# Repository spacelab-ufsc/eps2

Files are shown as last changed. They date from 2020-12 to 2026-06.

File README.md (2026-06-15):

<h1 align="center">
	ELECTRICAL POWER SYSTEM 2.0 (EPS2)
	<br>
</h1>

<p align="center">
    <!-- Versioning -->
    
    <!-- Releases -->
    
    <!-- Commits since the latest release -->
    
    <!-- Last commit -->
    
    <!-- Issues -->
    
    <!-- PRs -->
    
    <!-- Contributors -->
    
</p>

<details>
    <summary><b>Summary</b></summary>
    <ol>
        <li>
            <a href="#overview">Overview</a>
        </li>
        <li>
            <a href="#repository-organization">Repository Organization</a>
        </li>
        <li>
            <a href="#license">License</a>
        </li>
        <li>
            <a href="#releases">Releases</a>
        </li>
        <li>
            <a href="#notes">Notes</a>
        </li>
        <li>
            <a href="#references">References</a>
        </li>
    </ol>
</details>

## Repository Organization
`documentation`: Technical EPS2's documentation.

`firmware`: EPS2's firmware project (sources and configs).

`hardware`: EPS2's hardware project (sources and outputs).

## Overview
The **EPS2** [[1]](#1) was designed to collect, store, and distribute energy for GOLDS-UFSC and future SpaceLab missions, prioritizing practicality. It is highly based on the EPS1, used in FloripaSat-1 [[2]](#2). Supporting both 1U and 2U CubeSats, this EPS can interface with up to 10 solar panels attached to the structure. It operates the solar panels at their maximum power point (MPP) using the perturb and observe (P&O) technique to control three DC-DC converters at the input. The collected energy is stored in lithium-ion batteries, with power distribution managed by integrated DC-DC converters, generating 5V, 6V and 3.3V buses. This model features a microprocessor, the MSP430, which collects internal data (e.g., current, voltage, temperature) and manages their storage and transmission to the OBDH.

<p align="center">
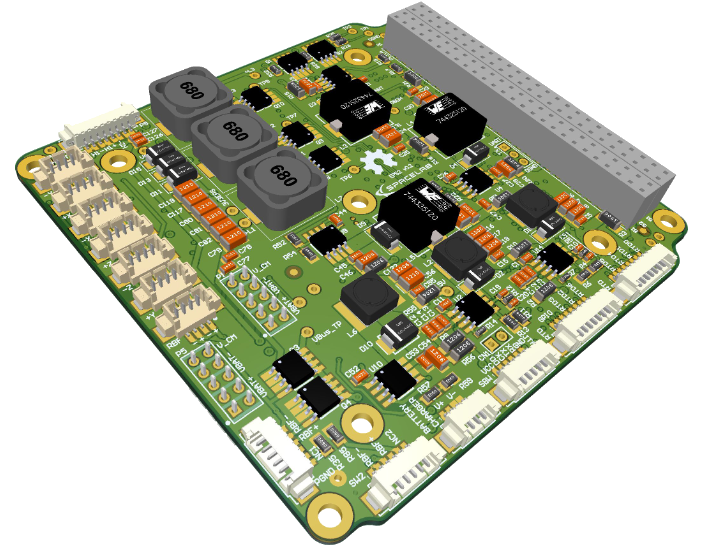
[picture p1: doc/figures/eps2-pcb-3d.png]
    
</p>

<p align="center">
    
    
    
</p>

## License
This project is open-source under three different licenses: CERN Open Hardware License v2.0 for hardware, GNU General Public License v3.0 for firmware, and CC BY-SA 4.0 for documentation.

## Releases
Releases are published after verifying that all components of the project — hardware, firmware, and documentation — are synchronized and compatible, ensuring functionality and cohesion. Using different versions of hardware, firmware, or documentation projects can lead to misunderstandings or unpredictable behavior. Please refer to the **documentation** for more details.

## Notes
For more info about the SpaceLab, access our [GitHub](https://github.com/spacelab-ufsc/spacelab), [Linkedin](https://br.linkedin.com/company/spacelab-ufsc) or our [website](https://spacelab.ufsc.br/en/home/).

## References
<a id="1">[1]</a> G. M. Marcelino, A. M. P. de Mattos, J. C. E. Barcellos, B. F. Ribeiro, L. O. Seman, E. M. Filho and E. A. Bezerra, "FloripaSat-2: An Open-Source Platform for CubeSats," in IEEE Embedded Systems Letters, vol. 16, no. 1, pp. 77-80, 2024, available at <a href="https://repositorio.ufsc.br/bitstream/handle/123456789/247559/PEEL2103-D.pdf?sequence=1&isAllowed=y"> this link</a>.

<a id="1">[2]</a> SpaceLab, "Electrical Power System (EPS)," in GitHub, 2019, available at <a href="https://github.com/spacelab-ufsc/eps"> this link</a>.

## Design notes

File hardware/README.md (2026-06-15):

<h1 align="center">
	EPS2 HARDWARE
	<br>
</h1>

<p align="center">
    <!-- Versioning -->
    
    <!-- Releases -->
    
    <!-- Hardware-related commits since the latest release -->
    
    <!-- Last hardware-related commit -->
    
    <!-- Hardware-related issues -->
    
    <!-- CAD tool used -->
    </a>
    <!-- License adopted -->
    </a>
</p>

<details>
    <summary><b>Summary</b></summary>
    <ol>
        <li>
            <a href="#overview">Overview</a>
        </li>
        <li>
            <a href="#license">License</a>
        </li>
        <li>
            <a href="#notes">Notes</a>
        </li>
        <li>
            <a href="#references">References</a>
        </li>
    </ol>
</details>

## Overview
The **EPS2** [[1]](#1) was designed to collect, store, and distribute energy for GOLDS-UFSC and future SpaceLab's missions, with a focus on practicality. It is higly based on the EPS1, used in FloripaSat-1 [[2]](#2). Then, it can be used in 1U and 2U CubeSats, this EPS can interface with up to 10 solar panels attached to the structure. It is also capable of operating the solar panels at their maximum power point (MPP). The collected energy is stored in lithium-ion batteries, and power distribution is managed by integrated DC-DC converters, generating 5V and 3.3V buses. This model is predominantly analog, enhancing its reliability in the challenging space environment. It also features redundancies in its energy harvesting unit (EHU) and power distribution unit (PDU).

<p align="center">
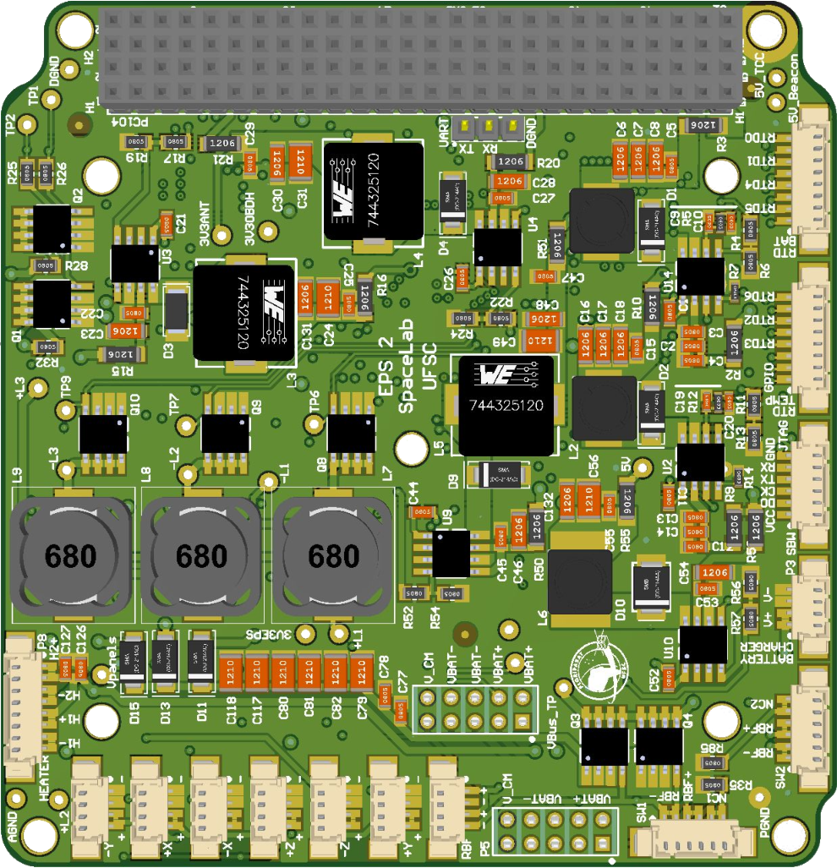
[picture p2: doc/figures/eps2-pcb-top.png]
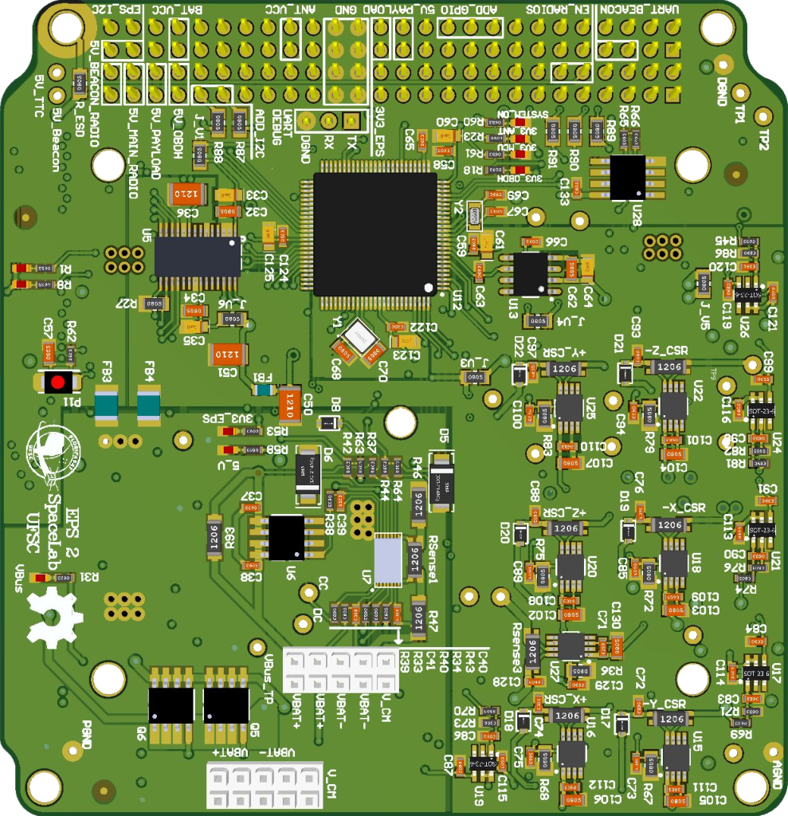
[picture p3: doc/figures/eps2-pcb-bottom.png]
    
</p>

### Architecture
The EPS2 includes an MSP430 microcontroller, which is responsible for reading various sensors and controlling its main units, such as the energy harvesting unit (EHU), power distribution unit (PDU), and power storage unit (PSU). It also features I²C and SPI interfaces for communication with the main modules of the satellite's service module. For more details, please refer to the **documentation**.

<p align="center">
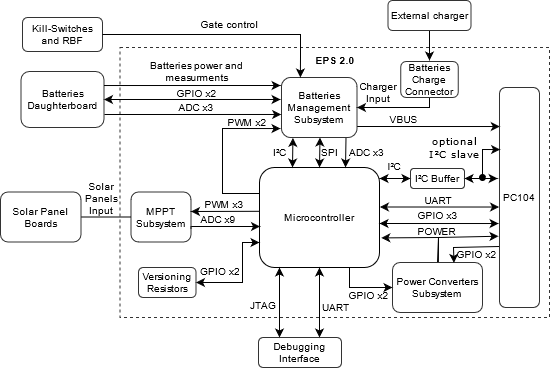
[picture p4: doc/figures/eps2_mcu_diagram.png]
    
</p>

### Development
#### Manufacture
The folder [fabrication](https://github.com/spacelab-ufsc/eps2/tree/master/hardware/fabrication) contains three "ready to go" files: the Gerbers and NC drill files for manufacturing the board, the BOM (Bill of Materials) with all required components, and the pick-and-place file for automated assembly. Additional files are available in the [outputs](https://github.com/spacelab-ufsc/eps2/tree/master/hardware/outputs) folder, which includes several useful files and documents such as 3D models, the bill of materials, schematics, layout prints, and draftsman files.

#### Assembly
The board has components that should not be soldered simultaneously. Please refer to the **documentation** in the assembly-related chapter for more details.

#### Power-on Procedure
To power on the board, you need to connect a battery (either the [BAT4C](https://github.com/spacelab-ufsc/battery-module-4c) model or the [BAT2C](https://github.com/spacelab-ufsc/battery-module-2c) model) or, at a minimum, emulate a battery using a power supply. For this, simply connect the power supply to provide 7.4V on `VBAT+`, GND on `VBAT-`, and 3.7V on `V_CM`. You can use the `P5` connector for this purpose. Refer to the **documentation** in the instructions-related chapter for more details.

## License
This project is open-source under the following license: CERN Open Hardware License v2.0.

## Notes
For more info about the SpaceLab, access our [GitHub](https://github.com/spacelab-ufsc/spacelab), [Linkedin](https://br.linkedin.com/company/spacelab-ufsc) or our [website](https://spacelab.ufsc.br/en/home/).

## References

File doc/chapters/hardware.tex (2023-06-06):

%
% hardware.tex
%
% Copyright (C) 2021 by SpaceLab.
%
% EPS 2.0 Documentation
%
% This work is licensed under the Creative Commons Attribution-ShareAlike 4.0
% International License. To view a copy of this license,
% visit http://creativecommons.org/licenses/by-sa/4.0/.
%

%
% \brief Hardware project chapter.
%
% \author Gabriel Mariano Marcelino <gabriel.mm8@gmail.com>
% \author Yan Castro de Azeredo <yan.ufsceel@gmail.com>
%
% \institution Universidade Federal de Santa Catarina (UFSC)
%
% \version 0.2.0
%
% \date 2021/02/16
%

\chapter{Hardware} \label{ch:hardware}

The EPS2 is a 4 layer 1.6mm thick PCB with FR-4 dielectric. The module does not have impedance control requirements; for this reason, the layer stackup has 1oz (0.0347mm) thickness in the inner and outer copper layers. The following sections describe the hardware design, interfaces, and standards in detail. Sections are divided by subsystem blocks, following the diagrams present on \autoref{fig:mcu-block-diagram} and \autoref{fig:power-block-diagram}. The \autoref{fig:pcb-top}, \autoref{fig:pcb-bottom} and \autoref{fig:pcb-side} presents the 3D rendered images of the top, bottom, and side views of the board, respectively.

\begin{figure}[!ht]
    \begin{center}
        
        \caption{Top side of the PCB.}
        \label{fig:pcb-top}
    \end{center}
\end{figure}

\begin{figure}[!ht]
    \begin{center}
        
        \caption{Bottom side of the PCB.}
        \label{fig:pcb-bottom}
    \end{center}
\end{figure}

\begin{figure}[!ht]
    \begin{center}
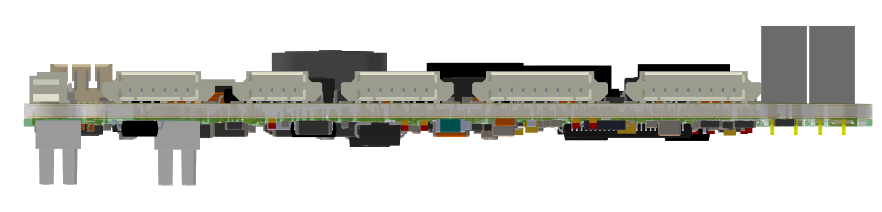
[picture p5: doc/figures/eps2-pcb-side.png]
        
        \caption{Side view of the PCB.}
        \label{fig:pcb-side}
    \end{center}
\end{figure}

\section{Interfaces}

The \autoref{fig:diagram-interfaces} presents the board interfaces, which consist of communication with other modules, debug access points, and internal peripherals. From the perspective of the microcontroller, there are 5 individual communication buses and the JTAG interface (Spy-Bi-Wire), in the \autoref{tab:interfaces}: A1-SPI (dedicated for RTD analog readings with ADS1248); A0-UART (dedicated for Beacon Radio); A2-UART (dedicated for debug); B0-I2C (dedicated for DS2777); B2-I2C (dedicated for OBDH); From the External Interface (IIP) can be acquired UART log messages for debugging via USB without the use of an external UART to USB converter. The SPI communication bus is a dedicated internal channel for the EPS MCU (master) to the ADS1248 (slave) ADC IC, the analog readings from BAT4C module (a.k.a Battery DaughterBoard) were also represented to show where the RTDs readings come from. \autoref{tab:usci-config} shows the interfaces configuration.

\begin{figure}[!ht]
    \begin{center}
        
        \caption{EPS interfaces diagram.}
        \label{fig:diagram-interfaces}
    \end{center}
\end{figure}

\begin{table}[!h]
    \centering
    \begin{tabular}{lrrr}
        \toprule[1.5pt]
        \textbf{Peripheral}     & \textbf{USCI} & \textbf{Protocol} & \textbf{Comm. Protocol} \\
        \midrule
        ADS1248                 & A1            & SPI               & - \\
        Beacon Radio            & A0            & UART              & - \\
        PC (log messages)       & A2            & UART              & ANSI messages \\
        DS2777                  & B0            & I$^{2}$C          & - \\
        OBDH                    & B2            & I$^{2}$C          & FSP \\
        External Interface      & -             & JTAG              & Spy-Bi-Wire \\
        \bottomrule[1.5pt]
    \end{tabular}
    \caption{Boards interfaces.}
    \label{tab:interfaces}
\end{table}

\section{Microcontroller}

The MCU consists of a CPU, RAM, and Flash Memory (used for program storage and non-volatile status registers). The chosen MCU is a low power 16-bit RISC (\textit{MSP430F6659IPZR}) from Texas Instruments\cite{msp430f6659}. The \autoref{tab:msp430-summary} presents a summary of the main available features and \autoref{fig:msp430-diagram} shows the internal subsystems, descriptions, and peripherals. The microcontroller interfaces, configurations, and auxiliary components are described in the following topics.

\begin{table}[!h]
    \centering
    \begin{tabular}{cllllllll}
        \toprule[1.5pt]
        \textit{Flash} & \textit{SRAM} & \textit{Timers} & \textit{USCI} & \textit{ADC} & \textit{DAC} & \textit{GPIO} \\
        \midrule
        512KB  & 64KB  & 2  & 6 (SPI / I2C / UART)  & 12  & 2  & 74           \\
        \bottomrule[1.5pt]
    \end{tabular}
    \caption{Microcontroller features summary.}
    \label{tab:msp430-summary}
\end{table}

\begin{figure}[!ht]
    \begin{center}
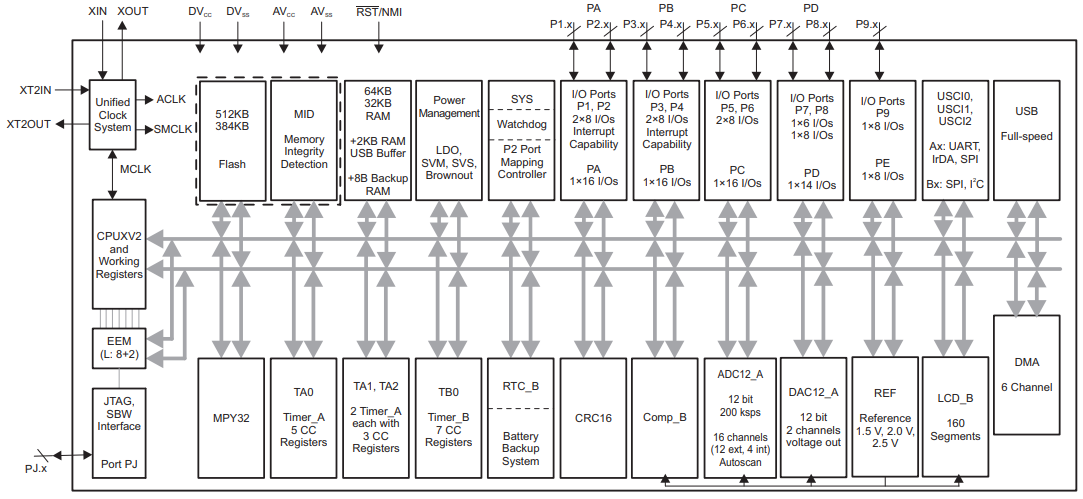
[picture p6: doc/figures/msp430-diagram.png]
        
        \caption{Microcontroller internal diagram.}
        \label{fig:msp430-diagram}
    \end{center}
\end{figure}

\subsection{Interfaces Configuration}

The microcontroller has 6 Universal Serial Communication Interfaces (USCI) that can be configured to operate with different protocols and parameters. The \autoref{tab:usci-config} describes each interface configuration.

\begin{table}[!h]
    \centering
    \begin{tabular}{lrrrrl}
        \toprule[1.5pt]
        \textit{Interface} & \textit{Protocol (Index)} & \textit{Mode} & \textit{Word Length} & \textit{Data Rate} & \textit{Configuration} \\
        \midrule
        USCI\_A0           & UART0                     & -             & 8 bits               & 9600 bps           & Stop bits: 1 \\
                           &                           &               &                      &                    & Parity: None \\
        USCI\_A1           & SPI                       & Master        & 8 bits               & TBD                & Phase: High \\
                           &                           &               &                      &                    & Polarity: Low \\
        USCI\_A2           & UART1                     & -             & 8 bits               & 9600 bps           & Stop bits: 1 \\
                           &                           &               &                      &                    & Parity: None \\
        USCI\_B0           & I2C0                      & Master        & 8 bits               & 100 kbps           & Adr. len: 7 bits \\
        USCI\_B2           & I2C1                      & Slave         & 8 bits               & 100 kbps           & Address value: 0x36 \\
        \bottomrule[1.5pt]
    \end{tabular}
    \caption{USCI configuration.}
    \label{tab:usci-config}
\end{table}

\subsection{Voltage Reference}

To generate the 3 volts reference for the MCU internal ADC, the EPS uses a \textit{595-REF5025AQDRQ1} chip.
Its circuit schematic can be seen in \autoref{fig:voltage-reference-circuit-schematic} and location on the PCB in \autoref{fig:voltage-reference-circuit-3d}.

\begin{figure}[!ht]
    \begin{center}
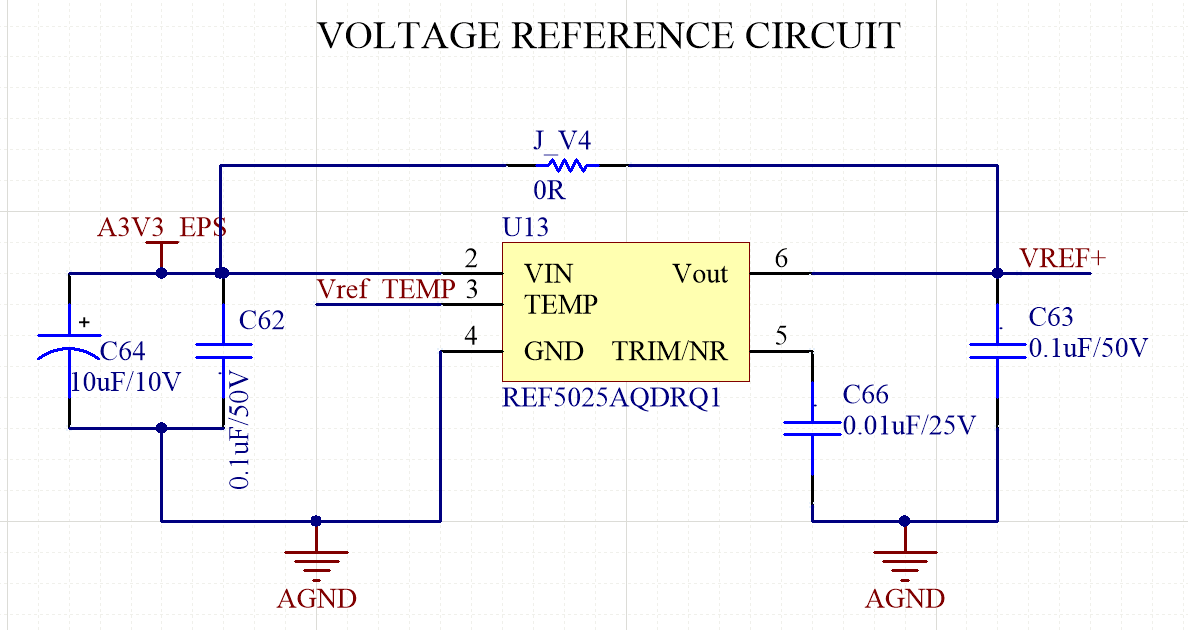
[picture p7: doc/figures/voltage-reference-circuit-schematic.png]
        
        \caption{Voltage reference circuit for EPS MCU schematic circuit.}
        \label{fig:voltage-reference-circuit-schematic}
    \end{center}
\end{figure}

\begin{figure}[!ht]
    \begin{center}
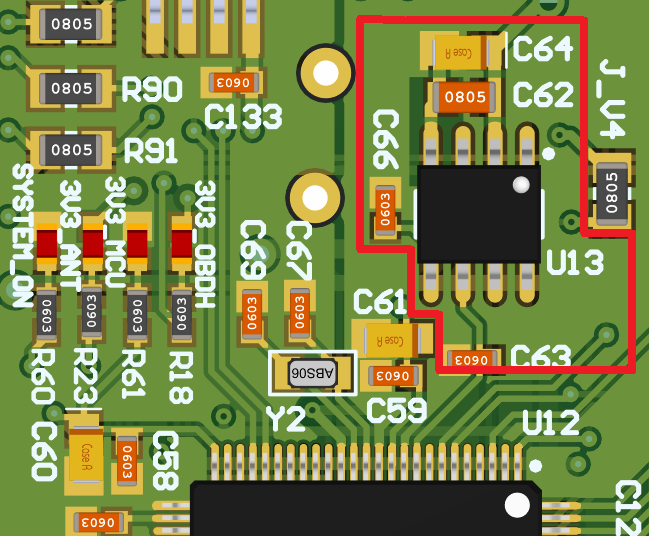
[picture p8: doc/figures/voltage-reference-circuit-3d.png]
        
        \caption{Voltage reference circuit for EPS MCU on the PCB.}
        \label{fig:voltage-reference-circuit-3d}
    \end{center}
\end{figure}

\subsection{Clocks Configuration}

Besides the internal clock sources, the microcontroller has two dedicated clock inputs for external crystals: the main clock and the auxiliary clock inputs. There are a 32MHz (\textit{ABM8X-102-32.000MHZ-T}) and a 32.769kHz (\textit{ECS-.327-12.5-34S-TR}) crystals connected to these inputs, respectively. The first source is used for generating the Master Clock (MCLK) and the Subsystem Master Clock (SMCLK), which are used by the CPU and the internal peripheral modules. The second source is used for generating the Auxiliary Clock (ACLK) that handles the low-power modes and might be used for peripherals.

\subsection{Pinout}

An illustration of the microcontroller pinout positions can be seen in the \autoref{fig:msp430-pinout-positions}. The \autoref{tab:mcu-pinout} presents all the EPS 2.0 microcontroller pins assignments.

\begin{figure}[!ht]
    \begin{center}
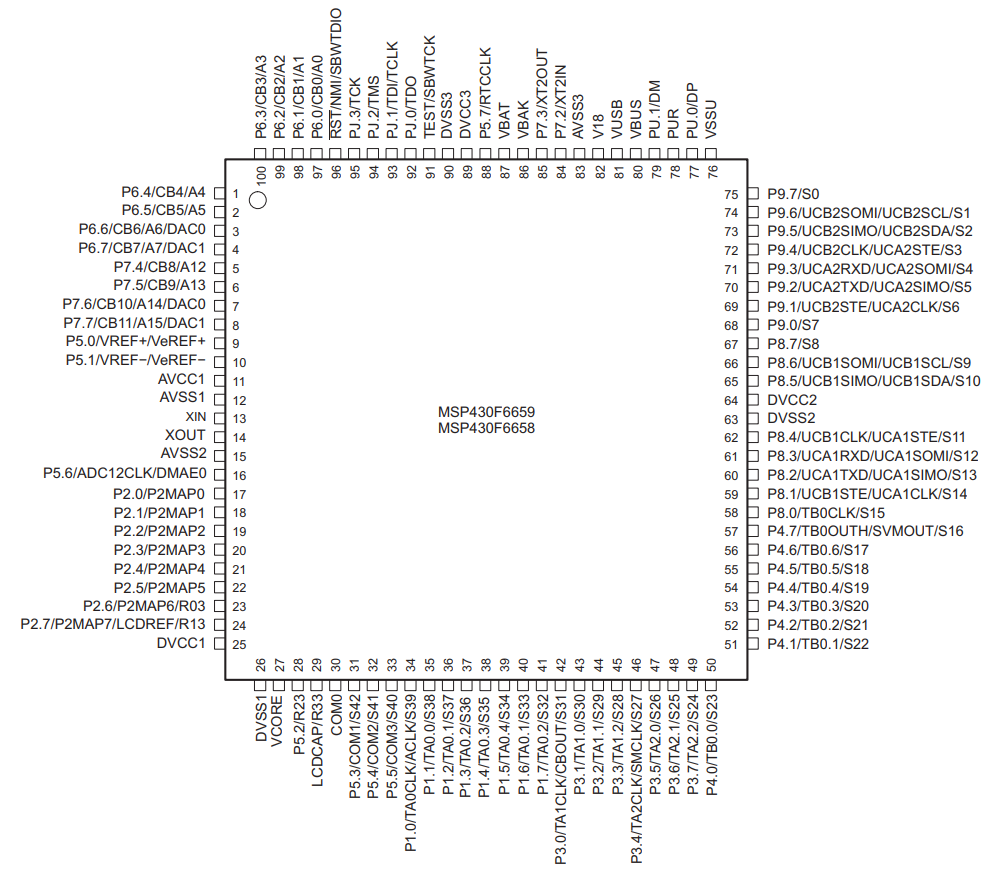
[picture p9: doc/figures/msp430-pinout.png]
        
        \caption{Microcontroller pinout positions.}
        \label{fig:msp430-pinout-positions}
    \end{center}
\end{figure}

\begin{longtable}{lcl}
    \toprule[1.5pt]
    \textit{Pin Code} & \textit{Pin Number} & \textit{Signal}       \\
    \midrule
    P1.0              & 34                  & -                 \\
    P1.1              & 35                  & -                 \\
    P1.2              & 36                  & -                 \\
    P1.3              & 37                  & EN\_5V\_PAYLOADS  \\
    P1.4              & 38                  & -             \\
    P1.5              & 39                  & BAT\_GPIO1    \\
    P1.6              & 40                  & BAT\_GPIO2    \\
    P1.7              & 41                  & -             \\
    \midrule
    P2.0              & 17                  & PIO           \\
    P2.1              & 18                  & I2C0\_SDA     \\
    P2.2              & 19                  & I2C0\_SCL     \\
    P2.3              & 20                  & PC104\_GPIO2  \\
    P2.4              & 21                  & UART\_EPS\_TX\_BEACON\_RX     \\
    P2.5              & 22                  & UART\_EPS\_RX\_BEACON\_TX     \\
    P2.6              & 23                  & PC104\_GPIO1                  \\            
    P2.7              & 24                  & PC104\_GPIO0                   \\
    \midrule
    P3.0              & 42                  & -                     \\
    P3.1              & 43                  & -                     \\
    P3.2              & 44                  & HEATER2\_PWM          \\
    P3.3              & 45                  & HEATER1\_PWM          \\
    P3.4              & 46                  & VERSION\_BIT0         \\
    P3.5              & 47                  & VERSION\_BIT1         \\
    P3.6              & 48                  & -                     \\
    P3.7              & 49                  & -                     \\
    \midrule
    P4.0              & 50                  & -                     \\
    P4.1              & 51                  & MPPT\_PWM\_1          \\
    P4.2              & 52                  & MPPT\_PWM\_2          \\
    P4.3              & 53                  & MPPT\_PWM\_3          \\
    P4.4              & 54                  & -                     \\
    P4.5              & 55                  & -                     \\
    P4.6              & 56                  & -                     \\
    P4.7              & 57                  & -                     \\
    \midrule
    P5.0              & 9                   & VREF                  \\
    P5.1              & 10                  & AGND                  \\
    P5.2              & 28                  & -                     \\
    P5.3              & 31                  & SYSTEM\_\_FAULT\_LED  \\
    P5.4              & 32                  & SYSTEM\_ON           \\
    P5.5              & 33                  & -                     \\
    P5.6              & 16                  & -                     \\
    P5.7              & 88                  & -                     \\
    \midrule
    P6.0              & 97                  & ADC1\_$+$Y\_SOLAR\_PANEL\_CURRENT \\
    P6.1              & 98                  & ADC2\_$+$X\_SOLAR\_PANEL\_CURRENT \\
    P6.2              & 99                  & ADC3\_$-$X\_SOLAR\_PANEL\_CURRENT \\
    P6.3              & 100                 & ADC4\_$+$Z\_SOLAR\_PANEL\_CURRENT \\
    P6.4              & 1                   & ADC5\_$-$Z\_SOLAR\_PANEL\_CURRENT \\
    P6.5              & 2                   & ADC6\_$+$Y\_SOLAR\_PANEL\_CURRENT \\
    P6.6              & 3                   & ADC7\_EPS\_TTC\_XCVR\_CURRENT \\
    P6.7              & 4                   & ADC\_MAIN\_POWER\_BUSS\_VOLTAGE \\
    \midrule
    P7.2              & 84                  & XT2\_N                \\
    P7.3              & 85                  & XT2\_P                \\
    P7.4              & 5                   & ADC1\_$-$Y\_$+$X\_SOLAR\_PANEL\_VOLTAGE \\
    P7.5              & 6                   & ADC2\_$-$X\_$+$Z\_SOLAR\_PANEL\_VOLTAGE \\
    P7.6              & 7                   & ADC3\_$-$Z\_$+$Y\_SOLAR\_PANEL\_VOLTAGE \\
    P7.7              & 8                   & ADC\_SOLAR\_PANELS\_TOTAL\_VOLTAGE \\
    \midrule
    P8.0              & 58                  & -                     \\
    P8.1              & 59                  & RTD\_SCLK             \\
    P8.2              & 60                  & RTD\_DIN              \\
    P8.3              & 61                  & RTD\_DOUT             \\
    P8.4              & 62                  & RTD\_RESET            \\
    P8.5              & 65                  & RTD\_CS               \\
    P8.6              & 66                  & RTD\_START            \\
    P8.7              & 67                  & RTD\_DRDY             \\
    \midrule
    P9.0              & 68                  & -                     \\
    P9.1              & 69                  & -                     \\
    P9.2              & 70                  & UART0\_TX             \\
    P9.3              & 71                  & UART0\_RX             \\
    P9.4              & 72                  & I2C1\_EN              \\
    P9.5              & 73                  & I2C1\_SDA             \\
    P9.6              & 74                  & I2C1\_SCL             \\
    P9.7              & 75                  & I2C1\_READY           \\
    \midrule
    PJ.0              & 92                  & -                     \\
    PJ.1              & 93                  & -                     \\
    PJ.2              & 94                  & -                     \\
    PJ.3              & 95                  & -                     \\
    \midrule
    -                 & 13                  & XT1IN                 \\
    -                 & 14                  & XT1OUT                \\
    -                 & 96                  & JTAG\_TDO\_TDI        \\
    -                 & 91                  & JTAG\_TCK             \\
    \bottomrule[1.5pt]
    \caption{Microcontroller pinout and assignments.}
    \label{tab:mcu-pinout}
\end{longtable}

\section{Batteries DaughterBoard}

Due to size restrictions the 4 cell batteries of the EPS2 were allocated to a daughterboard named Battery Module 4 Cells, a.k.a BAT4C\nomenclature{\textbf{BAT4C}}{\textit{Battery Module 4 Cells.}}\cite{bat4c}. Both boards 3D models are assembled together in a EDA tool as seen in \autoref{fig:eps2-pcb-3d-battery}. BAT4C is connected below EPS2 in a board-to-board connector; the female counterpart (\textit{BAT4CIPS1-105-01-S-D}) present on the EPS is seen in \autoref{fig:battery-connector} with its pinout present on \autoref{tab:battery-connector}.

For compatibility with the older version of the battery module, the same connector pads are present near the middle section of the PCB. If the BAT4C is to be used, the compatibility connector must not be soldered; more detail on \autoref{ch:assembly}. Also external connectors are used for temperature measurement and control with RTDs and heaters, more details can be seen on \autoref{rtd-picoblade} and \autoref{heater-picoblade}. 

\begin{figure}[!ht]
    \begin{center}
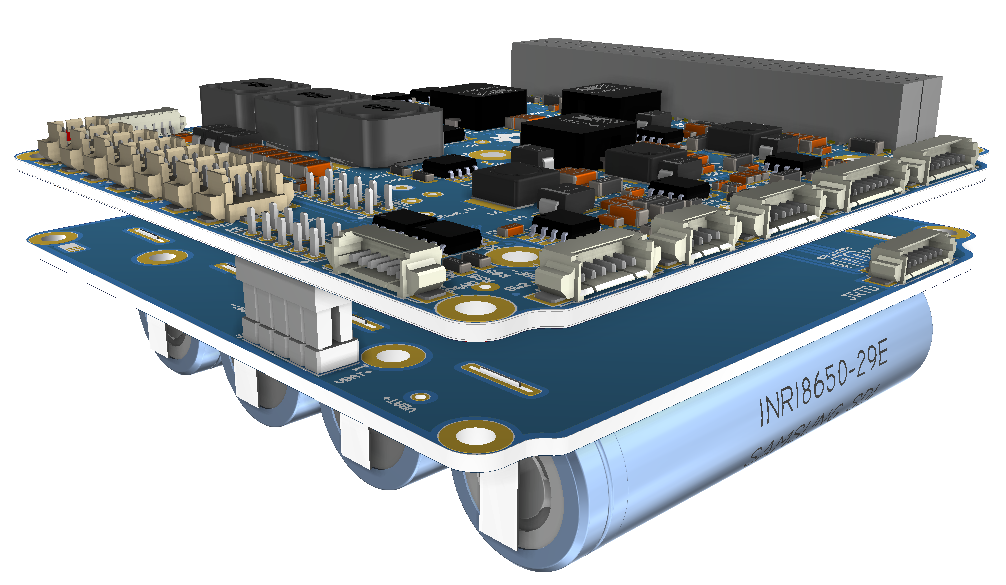
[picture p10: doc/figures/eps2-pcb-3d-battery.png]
        
        \caption{EPS2 and BAT4C 3D models assembled.}
        \label{fig:eps2-pcb-3d-battery}
    \end{center}
\end{figure}

\begin{figure}[!ht]
    \begin{center}
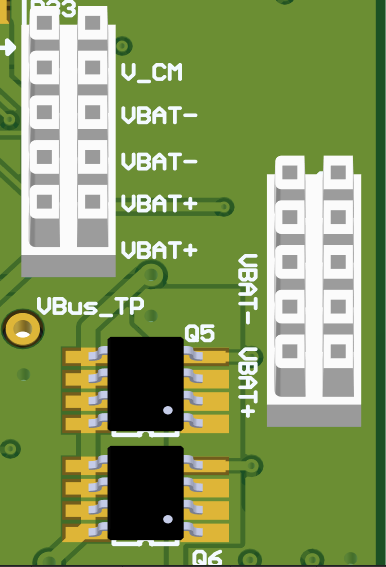
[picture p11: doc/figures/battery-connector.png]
        
        \caption{EPS2 battery connectors.}
        \label{fig:battery-connector}
    \end{center}
\end{figure}

\begin{table}[!h]
    \centering
    \begin{tabular}{cllll}
        \toprule[1.5pt]
        \textit{Pin} & \textit{Row} \\
        \midrule
        1            & $+$Vbat \\
        2            & $+$Vbat \\
        3            & $+$Vbat \\
        4            & $+$Vbat \\
        5            & $-$Vbat \\
        6            & $-$Vbat \\
        7            & $-$Vbat \\
        8            & $-$Vbat \\
        9            & Vbat\_Common \\
        10           & Vbat\_Common \\
        \bottomrule[1.5pt]
    \end{tabular}
    \caption{Battery connector pinout.}
    \label{tab:battery-connector}
\end{table}

\section{Solar Panels}

The energy harvesting system is based on solar energy conversion through ten solar panels attached to a 2U CubeSat structure. The solar panels are connected through six 4 pin PicoBlade connectors \textit{0533980471}. Because the EPS2 module has only six input connectors, four pairs of solar panels will be connected in parallel. The connection scheme of the solar panels is visible in \autoref{fig:diagram-solar-panels}. The power input connectors for the solar panels are described in \autoref{solar-panels-picoblades}.
\begin{figure}[!ht]
    \begin{center}
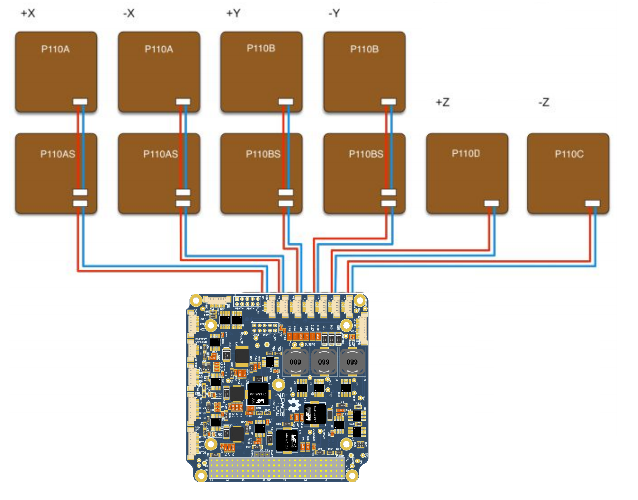
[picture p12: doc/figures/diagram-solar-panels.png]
        
        \caption{Solar panels connection to EPS2.}
        \label{fig:diagram-solar-panels}
    \end{center}
\end{figure}

\section{I2C Buffer}

The microcontroller I2C interface has a dedicated IC buffer, which improves the signal quality throughout the various connectors and offers reliability enhancements since it protects the bus in case of failures. This measure was adopted in all the satellite modules due to previous failures in I2C buses. Using this scheme, the modules connected through this protocol might have shared connections without losing performance or reliability. 

The buffer selected for this function is the Texas Instruments \textit{TCA4311}. Besides the I2C inputs and outputs, it features control and status signals connected to GPIOs in the microcontroller: an enable and an operation-ready status. Both inputs and outputs in these I2C lines have external pull-up resistors. Its circuit schematic can be seen \autoref{fig:i2c-buffer-circuit}.

\begin{figure}[!ht]
    \begin{center}
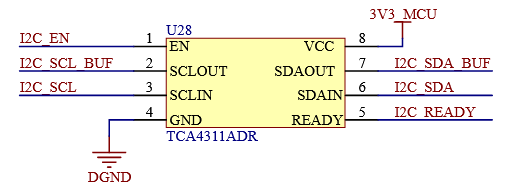
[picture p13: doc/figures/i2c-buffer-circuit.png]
        
        \caption{I2C buffer circuit.}
        \label{fig:i2c-buffer-circuit}
    \end{center}
\end{figure}

\section{MPPT Subsystem}

On the MPPT subsystem, the main components are the MPPT boost converters, solar panels, voltage and current sensors. These measurement circuits generate a voltage proportional to the measured variable, in a range accepted by the MCU internal ADC.

\subsection{MPPT Boost Converters}

The system has three boost converters, one for each couple of solar panels in parallel connection. Each one is a discrete boost with a \textit{MSS1278T-104MLD} inductor, a \textit{SI4166DY} MOSFET as the switch, and a \textit{B340LA-13-F} diode. There are six \textit{GRM32ER1E226KE15L} capacitors and two \textit{GRM216R71H103KA01D} capacitors connected in parallel in the boost output. The output filter is the same for all the converters, as their outputs are tied together. The MCU generates the control PWM signals at a frequency of 100 kHz.
One of the MPPT boosters circuit schematics can be seen in \autoref{fig:mppt-boosters-circuit-schematic} and the location of all three at the PCB in \autoref{fig:mppt-boosters-circuit-3d}.

\begin{figure}[!ht]
    \begin{center}
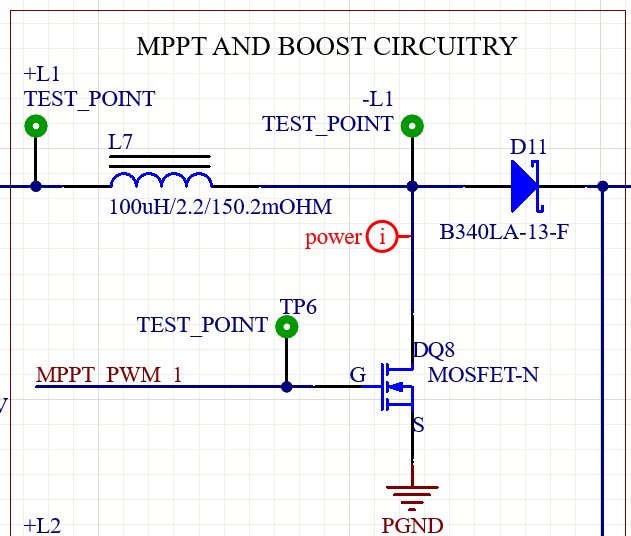
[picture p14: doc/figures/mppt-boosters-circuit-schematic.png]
        
        \caption{One of the MPPT boosters schematic circuit.}
        \label{fig:mppt-boosters-circuit-schematic}
    \end{center}
\end{figure}

\begin{figure}[!ht]
    \begin{center}
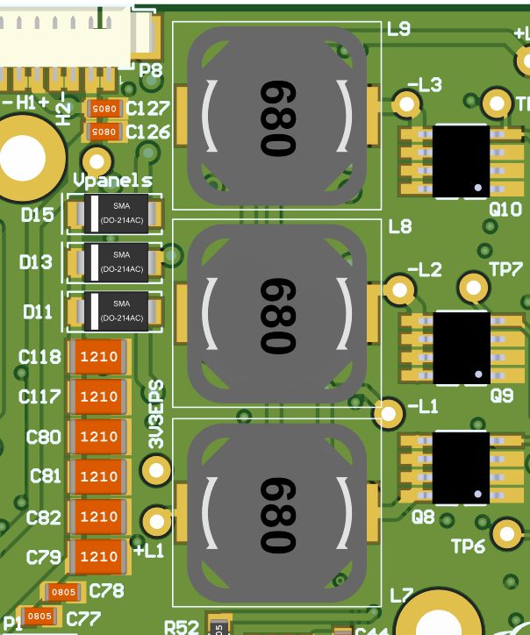
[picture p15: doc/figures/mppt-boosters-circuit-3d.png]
        
        \caption{MPPT boost converters circuit on the PCB.}
        \label{fig:mppt-boosters-circuit-3d}
    \end{center}
\end{figure}

\subsection{Solar Panels Current Measurement}

The main component of the solar panels' current measurement circuit is the \textit{MAX9934TAUA+} current sense amplifier. It generates an output current proportional to the differential input voltage. The gain is 25 $\mu$A/mV. It was considered a maximum current load sourced by two solar panels in parallel on the most optimist scenario of 1.5 A . To make the measurements possible, the current goes through 20 m$\Omega$, 0.5 \% resistors connected to the amplifier's inputs, and the outputs are connected to 3.3 k$\Omega$ resistors. The output voltage of the circuit is given by:

\begin{equation}
V_{out} = I_{load} \cdot R_{sense} \cdot G_{m} \cdot R_{out}
\end{equation}

The voltage drop in $R_{sense}$ generates a proportional $I_{out}$ on the IC of approximately 750 $\mu$A.
There are six current measurement circuits for the six sides of the CubeSat.
Two of the inputs of the solar panels circuit schematic can be seen in \autoref{fig:solar-panels-current-circuit-schematic} and the location of all six at the PCB in \autoref{fig:solar-panels-current-circuit-3d}.

\begin{figure}[!ht]
    \begin{center}
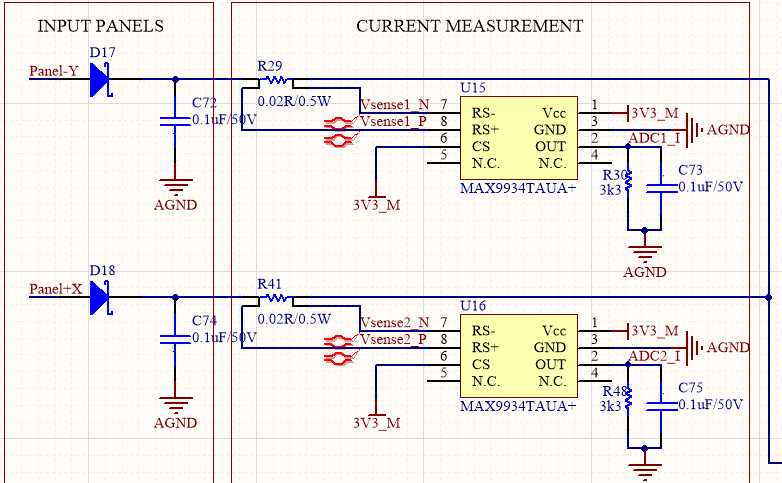
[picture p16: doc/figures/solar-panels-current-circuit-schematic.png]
        
        \caption{Solar panels $-$Y and $+$X input circuit schematic.}
        \label{fig:solar-panels-current-circuit-schematic}
    \end{center}
\end{figure}

\begin{figure}[!ht]
    \begin{center}
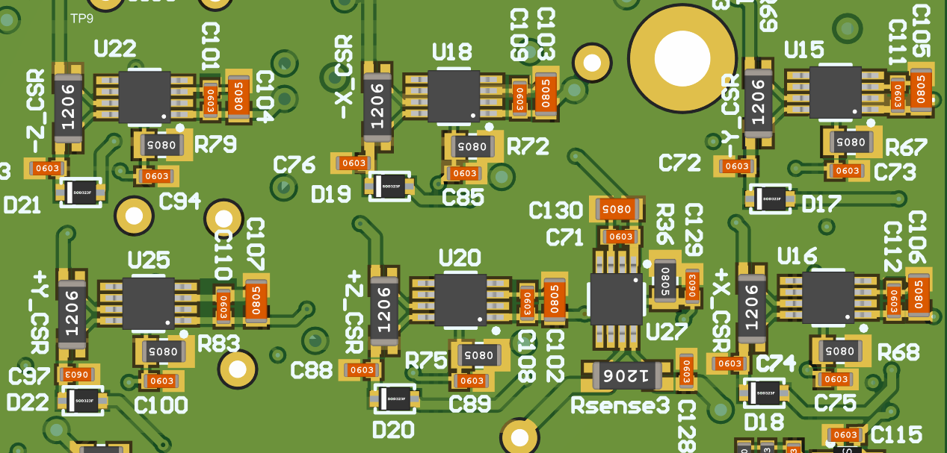
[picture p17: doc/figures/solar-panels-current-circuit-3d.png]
        
        \caption{Solar panels current measurement circuits on the PCB.}
        \label{fig:solar-panels-current-circuit-3d}
    \end{center}
\end{figure}

\subsection{Solar Panels Voltage Measurement}

The solar panels' voltage measurement circuit is composed by a voltage divider and an op-amp in a buffer configuration. The voltage divider comprises a 93.1 k$\Omega$ resistor and a 100 k$\Omega$ resistor. The op-amp is a \textit{TLV341AIDBVR} chip. The output voltage is given by:

\begin{equation}
V_{out} = V_{sp} \cdot \frac{R_{2}}{R_{1} + R_{2}}
\end{equation}

In total, there are three of these voltage measurement circuits, the solar panels' sides that are measured together are: $-$Y with $+$X, $-$X with $+$Z and $-$Z with $+$Y.
One voltage measurement circuit schematics can be seen in \autoref{fig:solar-panels-voltage-circuit-schematic}.

\begin{figure}[!ht]
    \begin{center}
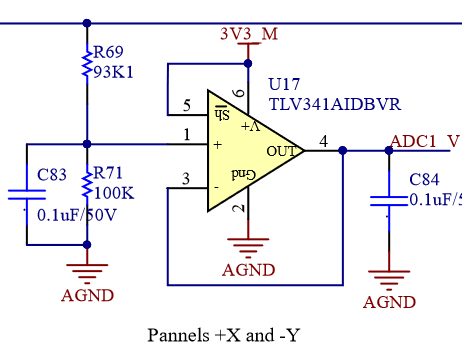
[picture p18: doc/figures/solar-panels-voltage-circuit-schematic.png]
        
        \caption{Solar panels $-$Y and $+$X voltage measurement circuit schematic.}
        \label{fig:solar-panels-voltage-circuit-schematic}
    \end{center}
\end{figure}

\section{Batteries Management Subsystem}

The main components of the batteries management subsystem are the battery control circuit, external ADC chip, solar panels and battery kill-switches, heater drivers and voltage sensors for the boosters output and main power bus. 

\subsection{Boost Converters Output Voltage Measurement}

The boost converters output voltage measurement circuit is very similar to the solar panels' voltages measurement circuit, except that the voltage divider is composed of a 300 k$\Omega$ resistor and a 100 k$\Omega$ resistor.
The schematic for the voltage measurement circuit of the solar panels can be seen again for reference in \autoref{fig:solar-panels-voltage-circuit-schematic}.

\subsection{Kill-Switches and Remove Before Flight}

These switches are used to separate the solar panels and the batteries from the load during pre-flight and launch. Each one is composed of two \textit{SI4403-CDY-T1-GE3} P-channel MOSFETs in parallel, as a redundancy.
The Kill-Switches and RBF\nomenclature{\textbf{RBF}}{\textit{Remove Before Flight.}} are interfaced on the EPS board via external PicoBlade cables to their respective external mechanisms.

RBF functions by simply making a short circuit in the pins of the pin header present on an external interface\cite{iip}, and for the kill-switches, it is required to press the spring buttons on the CubeSat structure; this is naturally done when the nanosatellite in integrated into the deployer.
On \autoref{kill-switches-picoblades} and \autoref{rbf-picoblade} it is showed the pinouts and locations for these connectors.

\subsection{Battery Monitor Circuit}

The batteries are monitored by the \textit{DS2777} chip. It measures several parameters and sends them to the EPS2 MCU via I2C protocol. The factory default value for its slave address is 0x59. Also, it automatically protects the batteries against short-circuits, overvoltage, and Undervoltage situations by switching two \textit{FDS6898AZ} MOSFETs.
Its circuit schematic can be seen in \autoref{fig:bms-circuit-schematic} and its location on the PCB in \autoref{fig:bms-circuit-3d}.

\begin{figure}[!ht]
    \begin{center}
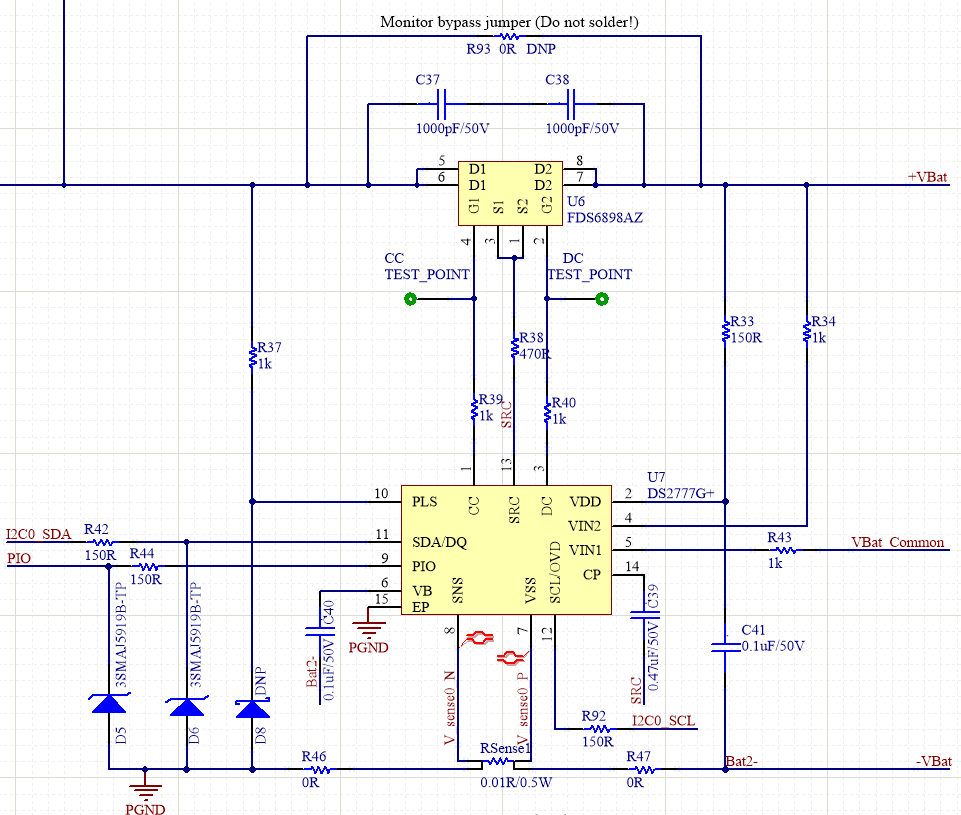
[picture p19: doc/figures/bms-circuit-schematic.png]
        
        \caption{Battery monitor circuit schematic.}
        \label{fig:bms-circuit-schematic}
    \end{center}
\end{figure}

\begin{figure}[!ht]
    \begin{center}
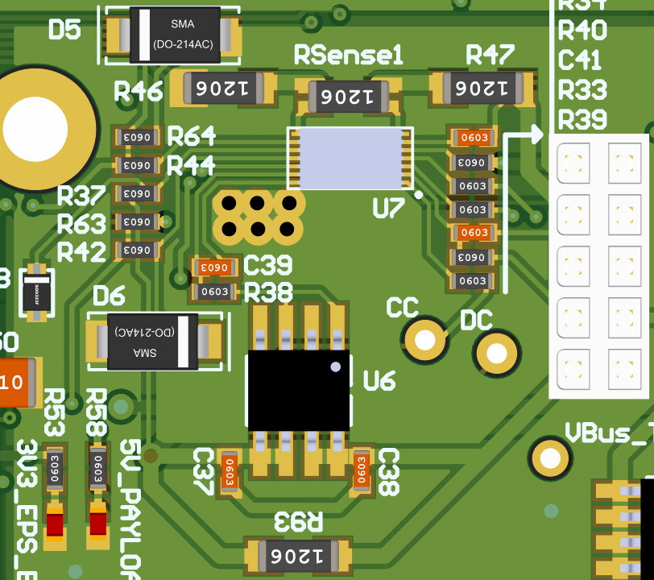
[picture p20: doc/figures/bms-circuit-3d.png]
        
        \caption{Battery monitor circuit on the PCB.}
        \label{fig:bms-circuit-3d}
    \end{center}
\end{figure}

\subsection{Main Power Bus Voltage Measurement}

The main power bus voltage measurement circuit is identical to the boost converters output voltage measurement circuit.
The schematic for the voltage measurement circuit of the solar panels can be seen again for reference in \autoref{fig:solar-panels-voltage-circuit-schematic}.

\subsection{External ADC}

The \textit{ADS1248} chip generates a precise reference current to the RTDs and samples the voltage proportional to the temperature established over the sensors. This voltage is converted to digital data and sent to the MCU via SPI protocol.
The location of the IC and its subcircuit can be seen in \autoref{fig:ads1248-circuit-3d}.

\begin{figure}[!ht]
    \begin{center}
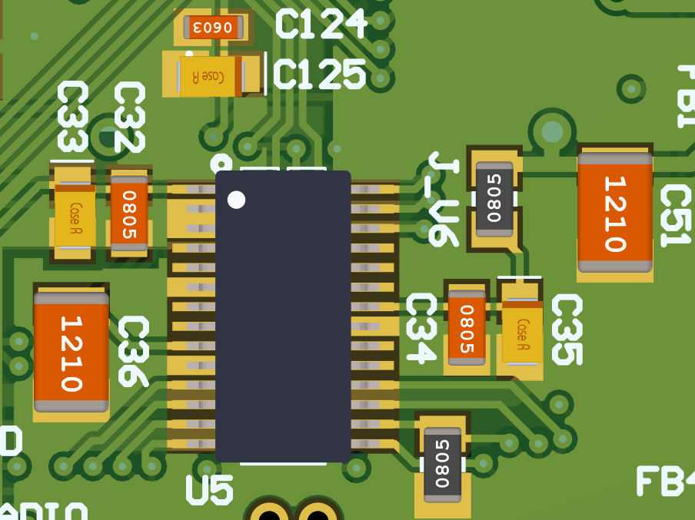
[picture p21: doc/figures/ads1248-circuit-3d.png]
        
        \caption{ADS1248 circuit on the PCB.}
        \label{fig:ads1248-circuit-3d}
    \end{center}
\end{figure}

\subsection{Heaters Drivers}

The drivers are chopper converters managed by the MCU, either switched to on/off or controlled with a PWM signal with a frequency of 50 kHz, depending on the mode of operation (detailed in chapter \autoref{ch:firmware}). The switches of the chopper converters are \textit{Si4010DY} MOSFETs.
Its circuit schematic can be seen in \autoref{fig:heaters-circuit-schematic} and location on the PCB in \autoref{fig:heaters-drivers-circuit-3d}.

\begin{figure}[!ht]
    \begin{center}
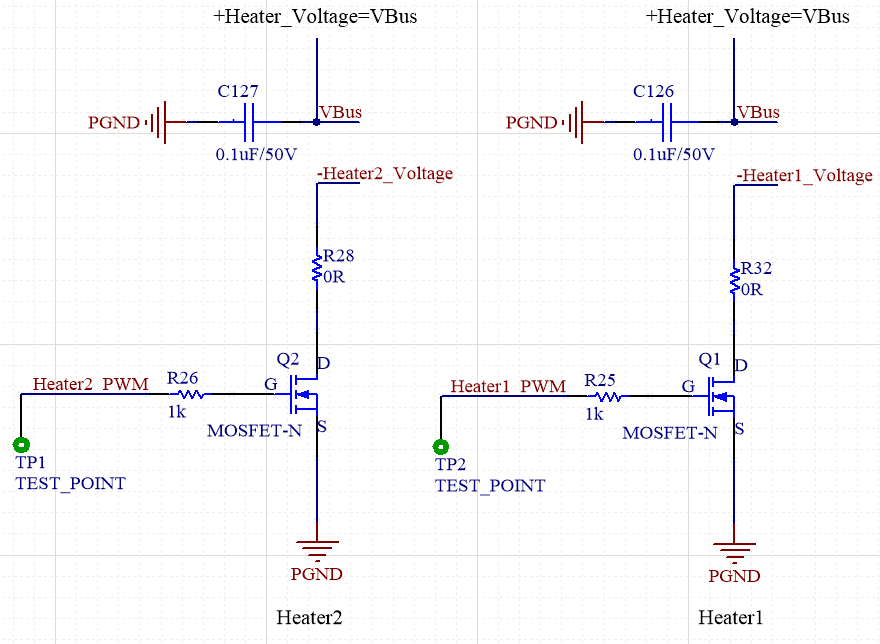
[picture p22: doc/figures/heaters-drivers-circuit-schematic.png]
        
        \caption{Heater drivers circuit schematic.}
        \label{fig:heaters-circuit-schematic}
    \end{center}
\end{figure}

\begin{figure}[!ht]
    \begin{center}
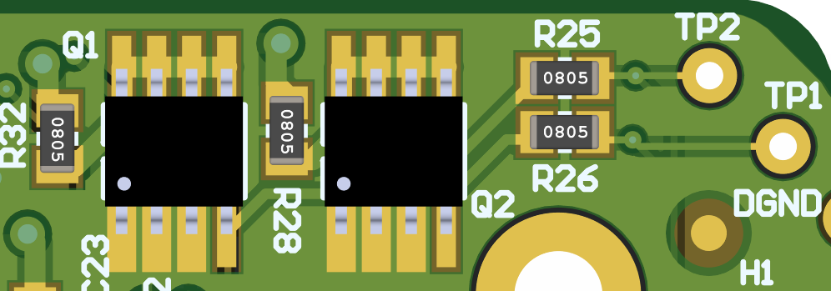
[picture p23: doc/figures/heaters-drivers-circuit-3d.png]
        
        \caption{Heater drivers circuit on the PCB.}
        \label{fig:heaters-drivers-circuit-3d}
    \end{center}
\end{figure}

\section{Power Converters Subsystem}

The EPS2 has 6 integrated buck DC-DC regulators, all of which are powered from the main power bus. Some regulators are always enabled, and others can be enabled or disabled by the EPS2 or other modules.

\subsection{EPS/TTC Regulator}

To supply the TTC MCU (also called "Beacon MCU") and EPS2 MCU and its subcircuits a \textit{TPS5420QDRQ1} regulator is used, with an output voltage of 3.3 V and 2 A current capability. This regulator is always on.
The EPS/TTC circuit location on the PCB can be seen in \autoref{fig:eps-beacon-buck-circuit-3d}.

\begin{figure}[!ht]
    \begin{center}
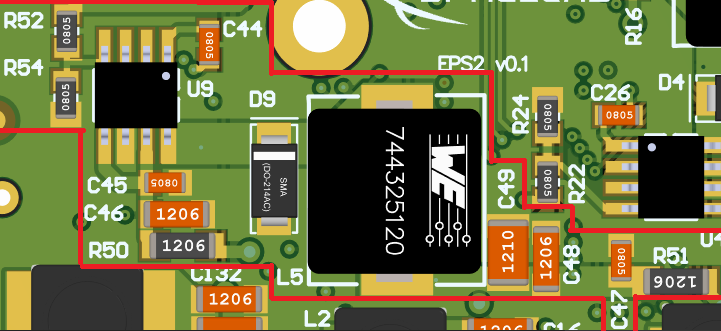
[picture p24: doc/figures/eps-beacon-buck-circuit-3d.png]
        
        \caption{EPS/TTC regulator circuit on the PCB.}
        \label{fig:eps-beacon-buck-circuit-3d}
    \end{center}
\end{figure}

There is also a current measurement of the output of the EPS/TTC regulator. It also uses a \textit{MAX9934TAUA+} current sense amplifier, but with a shunt resistor of 75 m$\Omega$, 0.5 \% and the output connected to a 4.02 k$\Omega$ resistor.
The circuit schematic is almost the same as \autoref{fig:solar-panels-current-circuit-schematic} only changing the resistors and capacitor values, its location on the PCB is the labeled U27 IC, and its passive components in \autoref{fig:solar-panels-current-circuit-3d}.

\subsection{OBDH Regulator}

The OBDH is powered by a \textit{TPS5410QDRQ1} regulator, with an output voltage of 3.3 V and 1 A current capability.
Its location on the PCB can be seen in \autoref{fig:obdh-buck-circuit-3d}.

\begin{figure}[!ht]
    \begin{center}
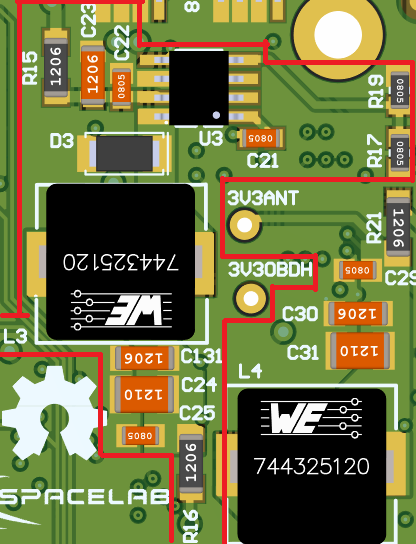
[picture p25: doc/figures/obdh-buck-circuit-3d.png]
        
        \caption{OBDH regulator circuit on the PCB.}
        \label{fig:obdh-buck-circuit-3d}
    \end{center}
\end{figure}

\subsection{Antenna Deployer Regulator}

The antenna deployment system has a dedicated regulator \textit{TPS5420QDRQ1}, with 3.3 V output voltage and 2 A current capability. This regulator is always on.
Its location on the PCB can be seen in \autoref{fig:ant-buck-circuit-3d}.

\begin{figure}[!ht]
    \begin{center}
        
        \caption{Antenna deployer regulator circuit on the PCB.}
        \label{fig:ant-buck-circuit-3d}
    \end{center}
\end{figure}

\subsection{Radio 0 Transceiver Regulator}

The radio 0 XCVR\nomenclature{\textbf{XCVR}}{\textit{Transceiver.}} responsible for the Downlink/Uplink of the CubeSat is powered by a \textit{TPS54540QDDARQ1} regulator, with an output voltage of 5V and 5A capability. The OBDH can enable/disable this regulator.
Its location on the PCB can be seen in \autoref{fig:main-radio-buck-circuit-3d}.

\begin{figure}[!ht]
    \begin{center}
        
        \caption{Main radio transceiver regulator circuit on the PCB.}
        \label{fig:main-radio-buck-circuit-3d}
    \end{center}
\end{figure}

\subsection{Radio 1 Transceiver Regulator}

The radio 1 XCVR responsible for a periodic data sent status of the CubeSat is powered by a \textit{TPS54540QDDARQ1} regulator, with 6V output voltage and 5A capability. The Beacon MCU can enable/disable this regulator.
Its location on the PCB can be seen in \autoref{fig:beacon-radio-buck-circuit-3d}.

\begin{figure}[!ht]
    \begin{center}
        
        \caption{Beacon radio transceiver regulator circuit on the PCB.}
        \label{fig:beacon-radio-buck-circuit-3d}
    \end{center}
\end{figure}

\subsection{Payloads Regulator}

A \textit{TPS5430QDDARQ1} regulator is used to power the payloads. It has an output voltage of 5 V and 3 A current capability. The EPS2 can enable/disable this regulator.
Its location on the PCB can be seen in \autoref{fig:payloads-buck-circuit-3d}.

\begin{figure}[!ht]
    \begin{center}
        
        \caption{Payloads regulator circuit on the PCB.}
        \label{fig:payloads-buck-circuit-3d}
    \end{center}
\end{figure}

\section{External Connectors} \label{external-connectors}

The EPS2 module is connected to the other modules using the PC104 bus. The solar panels, the kill switches, the remove before the flight, the RTDs, the heater, the batteries charger connector, and the JTAG pins are connected using Molex PicoBlade connectors. The EPS2 module also has a jumper that connects the MCU VCC to the JTAG VCC and a header to debug the board via UART protocol.

In the following sections, each connector is detailed, with a picture showing the location on the EPS2 PCB and a table explaining each pin function.

\subsection{PC104} \label{PC104}

The connector PC-104 is a junction of two double-row 28H headers (\textit{SSW-126-01-G-D}). These connectors create a solid 104-pin interconnection across the different satellite modules. The \autoref{fig:pc104-scheme} shows the PC-104 interface from the bottom side of the PCB, which allows visualizing the simplified label scheme in the board. Also, the \autoref{tab:pc104-pins} provides the connector pinout\footnote{This pinout is simplified since additional interfaces were omitted. Refer to \textit{option sheet} in chapter \ref{ch:assembly}.} for the pins that are connected to the module. 

\begin{figure}[!ht]
    \begin{center}
        
        \caption{Bottom view of PC-104 and simplified labels.}
        \label{fig:pc104-scheme}
    \end{center}
\end{figure}

\begin{table}[!h]
    \centering
    \begin{tabular}{cllll}
        \toprule[1.5pt]
        \textit{Pin [A-B]} & \textit{H1A}     & \textit{H1B}     & \textit{H2A}  & \textit{H2B}  \\
        \midrule
        1-2                & -                & -                & -             & -             \\
        3-4                & -                & -                & -             & -             \\
        5-6                & -                & -                & UART\_RX      & -             \\
        7-8                & -                & -                & UART\_TX      & -             \\
        9-10               & -                & EN\_PWR\_5       & -             & -             \\
        11-12              & -                & EN\_PWR\_6       & -             & -             \\
        13-14              & -                & -                & -             & -             \\
        15-16              & -                & -                & -             & -             \\
        17-18              & -                & -                & -             & -             \\
        19-20              & -                & -                & -             & -             \\
        21-22              & -                & -                & -             & -             \\
        23-24              & -                & -                & -             & -             \\
        25-26              & -                & -                & PWR\_4\_5V    & PWR\_4\_5V    \\
        27-28              & -                & -                & PWR\_7\_3V3   & PWR\_7\_3V3   \\
        29-30              & GND              & GND              & GND           & GND           \\
        31-32              & GND              & GND              & GND           & GND           \\
        33-34              & -                & -                & -             & -             \\
        35-36              & -                & -                & PWR\_1\_3V3   & PWR\_1\_3V3   \\
        37-38              & -                & -                & -             & -             \\
        39-40              & -                & -                & -             & -             \\
        41-42              & -                & -                & -             & -             \\
        43-44              & -                & -                & -             & -             \\
        45-46              & PWR\_2\_3V3      & PWR\_2\_3V3      & PWR\_3\_BAT   & PWR\_3\_BAT   \\
        47-48              & PWR\_4\_5V       & PWR\_4\_5V       & -             & -             \\
        49-50              & PWR\_5\_5V       & PWR\_5\_5V       & I2C\_SDA      & -             \\
        51-52              & PWR\_6\_6V       & PWR\_6\_6V       & I2C\_SCL      & -             \\
        \bottomrule[1.5pt]
    \end{tabular}
    \caption{PC-104 connector pinout.}
    \label{tab:pc104-pins}
\end{table}

\begin{table}[!h]
    \centering
    \begin{tabular}{lL{0.29\textwidth}L{0.47\textwidth}}
        \toprule[1.5pt]
        \textbf{Signal}  & \textbf{Pin(s)}            & \textbf{Description} \\
        \midrule
        GND              & H1-29, H1-30, H1-31, H1-32, H2-29, H2-30, H2-31, H2-32 & Ground reference \\
        PWR\_1\_3V3      & H2-35, H2-36               & Power bus 1, 3.3 V, 2 A max. \\
        PWR\_2\_3V3      & H1-45, H1-46               & Power bus 2, 3.3 V, 1 A max. \\
        PWR\_3\_BAT      & H2-45, H2-46               & Power bus 3, battery terminals (+) \\
        PWR\_4\_5V       & H1-47, H1-48, H2-25, H2-26 & Power bus 4, 5 V, 3 A max. \\
        PWR\_5\_5V       & H1-49, H1-50               & Power bus 5, 5 V, 5 A max. \\
        PWR\_6\_6V       & H1-51, H1-52               & Power bus 6, 6 V, 5 A max. \\
        PWR\_7\_3V3      & H2-27, H2-28               & Power bus 7, 3.3 V, 2 A max. \\
        I2C\_SDA         & H2-49                      & Primary communication bus (data signal) \\
        I2C\_SCL         & H2-51                      & Primary communication bus (clock signal) \\
        UART\_RX         & H2-5                       & Secondary communication bus (RX) \\
        UART\_TX         & H2-7                       & Secondary communication bus (TX) \\
        EN\_PWR\_5       & H1-10                      & Enable signal of the power bus 5 \\
        EN\_PWR\_6       & H1-12                      & Enable signal of the power bus 6 \\
        \bottomrule[1.5pt]
    \end{tabular}
    \caption{PC-104 bus signal description.}
    \label{tab:pc104-signals}
\end{table}

\subsection{Solar Panels PicoBlades} \label{solar-panels-picoblades}

Six PicoBlade connectors can be connected to solar panels. Each one of them is to be used with its respective positive or negative cartesian axis reference label: X, Y, or Z. Note that the total current for each individual PicoBlade pin must not exceed 1000mA; this means that the maximum current per connector is 2000mA.
Their pinout is shown in \autoref{tab:solar-panels-picoblades} and position on the PCB in \autoref{fig:solar-panels-picoblades}.

\begin{table}[!h]
    \centering
    \begin{tabular}{cl}
        \toprule[1.5pt]
        \textit{Pin} & \textit{Row} \\
        \midrule
        1            & Panel [side reference] positive input\\
        2            & Panel [side reference] positive input \\
        3            & PGND \\
        4            & PGND \\
        \bottomrule[1.5pt]
    \end{tabular}
    \caption{Solar panels PicoBlades pinout.}
    \label{tab:solar-panels-picoblades}
\end{table}

\begin{figure}[!ht]
    \begin{center}
        
        \caption{Solar panels power input connectors on the PCB.}
        \label{fig:solar-panels-picoblades}
    \end{center}
\end{figure}

\subsection{Kill-Switches PicoBlades} \label{kill-switches-picoblades}

There are two PicoBlade connectors to two separated kill-switch spring button mechanisms, one of which is illustrated in \autoref{fig:kill-switch-installed}. The connection is made by manually soldering and isolating with a heat shrink tube; the other end of the cable goes to PicoBlades of the EPS, their pinout is showed in \autoref{tab:kill-switches-picoblades} and position on the PCB in \autoref{fig:kill-switches-picoblades}.

\begin{figure}[!ht]
    \begin{center}
        
        \caption{Kill-switch spring button mechanism.}
        \label{fig:kill-switch-installed}
    \end{center}
\end{figure}

\begin{table}[!h]
    \centering
    \begin{tabular}{cl}
        \toprule[1.5pt]
        \textit{Pin} & \textit{Row} \\
        \midrule
        1            & Common \\
        2            & Common \\
        3            & NO\nomenclature{\textbf{NO}}{\textit{Normally open.}} \\
        4            & NO\nomenclature{\textbf{NO}}{\textit{Normally open.}} \\
        5            & NC\nomenclature{\textbf{NC}}{\textit{Normally closed.}} \\
        6            & NC\nomenclature{\textbf{NC}}{\textit{Normally closed.}} \\
        \bottomrule[1.5pt]
    \end{tabular}
    \caption{Kill-switches PicoBlades pinout.}
    \label{tab:kill-switches-picoblades}
\end{table}

\begin{figure}[!ht]
    \begin{center}
        
        \caption{Kill-switches PicoBlade connectors on the PCB.}
        \label{fig:kill-switches-picoblades}
    \end{center}
\end{figure}

\subsection{RBF PicoBlade} \label{rbf-picoblade}

The RBF PicoBlade interconnects the separation switches circuit on the EPS to be accessed in an external interface. Its pinout is shown in \autoref{tab:rbf-picoblade} and position on the PCB in \autoref{fig:rbf-picoblade}.

\begin{table}[!h]
    \centering
    \begin{tabular}{cl}
        \toprule[1.5pt]
        \textit{Pin} & \textit{Row} \\
        \midrule
        1            & $+$RBF \\
        2            & $-$RBF \\
        3            & $+$RBF \\
        4            & $-$RBF \\
        \bottomrule[1.5pt]
    \end{tabular}
    \caption{RBF PicoBlade pinout.}
    \label{tab:rbf-picoblade}
\end{table}

\begin{figure}[!ht]
    \begin{center}
        
        \caption{RBF PicoBlade connector on the PCB.}
        \label{fig:rbf-picoblade}
    \end{center}
\end{figure}

\subsection{RTDs PicoBlade} \label{rtd-picoblade}

EPS reads temperature from RTDs present in the BAT4C module with a external PicoBlade cable connected between both boards. The two connectors RTD1 and RTD2 pinouts, are shown in \autoref{tab:rbf-picoblade} and positions on the PCB in \autoref{fig:rtds-picoblades}.

\begin{table}[!h]
    \centering
    \begin{tabular}{cl}
        \toprule[1.5pt]
        \textit{Pin} & \textit{Row} \\
        \midrule
        RTD1 PicoBlade &  \\
        \midrule
        1            & BAT\_GPIO1   \\
        2            & BAT\_GPIO2   \\
        3            & RTD\_Common  \\
        4            & RTD\_RTD3    \\
        5            & RTD\_Common  \\
        6            & RTD\_RTD2    \\
        7            & RTD\_Common  \\
        8            & RTD\_RTD6    \\
        \midrule
        RTD2 PicoBlade &  \\
        \midrule
        1            & RTD\_Common  \\
        2            & RTD\_RTD5    \\
        3            & RTD\_Common  \\
        4            & RTD\_RTD4    \\
        5            & RTD\_Common  \\
        6            & RTD\_RTD1    \\
        7            & RTD\_Common  \\
        8            & RTD\_RTD0    \\
        \bottomrule[1.5pt]
    \end{tabular}
    \caption{RBF PicoBlade pinout.}
    \label{tab:rbf-picoblade}
\end{table}

\begin{figure}[!ht]
    \begin{center}
        
        \caption{RTDs PicoBlade connectors on the PCB.}
        \label{fig:rtds-picoblades}
    \end{center}
\end{figure}

\subsection{Heater PicoBlade} \label{heater-picoblade}

A external PicoBlade cable also brings the PWM signals that control the heaters present on the BAT4C module. The connector pinout is showed in \autoref{tab:heater-picoblade} and positions on the PCB in \autoref{fig:heaters-picoblade}.

\begin{table}[!h]
    \centering
    \begin{tabular}{cl}
        \toprule[1.5pt]
        \textit{Pin} & \textit{Row} \\
        \midrule
        1            & $-$Heater1\_Voltage \\
        2            & $-$Heater1\_Voltage \\
        3            & VBUS \\
        4            & VBUS \\
        5            & $-$Heater2\_Voltage \\
        6            & $-$Heater2\_Voltage \\
        7            & VBUS \\
        8            & VBUS \\
        \bottomrule[1.5pt]
    \end{tabular}
    \caption{Heater PicoBlade pinout.}
    \label{tab:heater-picoblade}
\end{table}

\begin{figure}[!ht]
    \begin{center}
        
        \caption{Heaters PicoBlade connector on the PCB.}
        \label{fig:heaters-picoblade}
    \end{center}
\end{figure}

\subsection{External Batteries Charger PicoBlade} \label{external-charge-picoblade}

When the EPS and BAT4C are assembled, the batteries can be charged from a PicoBlade connector, which is accessed in an external interface. The same current restriction as for the solar panels' connectors is applied here; the external batteries charger PicoBlade must not exceed 2000mA. The connector pinout is shown in \autoref{tab:batteries-picoblade} and position on the PCB in \autoref{fig:batteries-picoblade}.

\begin{table}[!h]
    \centering
    \begin{tabular}{cl}
        \toprule[1.5pt]
        \textit{Pin} & \textit{Row} \\
        \midrule
        1            & V\_Charging\_Batteries \\
        2            & V\_Charging\_Batteries \\
        3            & PGND \\
        4            & PGND \\
        \bottomrule[1.5pt]
    \end{tabular}
    \caption{External batteries charger PicoBlade pinout.}
    \label{tab:batteries-picoblade}
\end{table}

\begin{figure}[!ht]
    \begin{center}
        
        \caption{External batteries charger PicoBlade connector on the PCB.}
        \label{fig:batteries-picoblade}
    \end{center}
\end{figure}

\subsection{JTAG PicoBlade} \label{jtag-picoblade}

The EPS module can be programmed and debugged through its JTAG PicoBlade connector as shown in \autoref{fig:jtag-picoblade}. 
The pin header labeled CN1 is a jumper for shorting the power from the flash emulator tool to the 3V3 power used for the EPS MCU and subcircuits.
This feature enables powering the board partially using MSP-FET, be advised to leave this connector open if the EPS is powered from other means; for more details, see \autoref{ch:instructions}.
The JTAG connector pinout is shown in \autoref{tab:jtag-picoblade}.

\begin{table}[!h]
    \centering
    \begin{tabular}{cl}
        \toprule[1.5pt]
        \textit{Pin} & \textit{Row} \\
        \midrule
        1            & 3V3\_MCU \\
        2            & TDO \\
        3            & TCK \\
        4            & UART\_Debug\_Tx \\
        5            & UART\_Debug\_Rx \\
        6            & DGND \\
        \bottomrule[1.5pt]
    \end{tabular}
    \caption{JTAG PicoBlade pinout.}
    \label{tab:jtag-picoblade}
\end{table}

\begin{figure}[!ht]
    \begin{center}
        
        \caption{JTAG PicoBlade connector on the PCB.}
        \label{fig:jtag-picoblade}
    \end{center}
\end{figure}

\newpage

\subsection{Debug UART Pin Header} \label{uart-pin-header}

A pin header can be easily accessed with jumper wires for debugging via UART using log messages during the test phase. This connector is not meant to be soldered in the flight model of the EPS. The connector pinout is shown in \autoref{tab:uart-pin-header} and position on the PCB in \autoref{fig:uart-pin-header}.

\begin{table}[!h]
    \centering
    \begin{tabular}{cl}
        \toprule[1.5pt]
        \textit{Pin} & \textit{Row} \\
        \midrule
        1            & UART\_Debug\_Tx \\
        2            & UART\_Debug\_Rx \\
        3            &  DGND \\
        \bottomrule[1.5pt]
    \end{tabular}
    \caption{Debug UART pin header pinout.}
    \label{tab:uart-pin-header}
\end{table}

\begin{figure}[!ht]
    \begin{center}
        
        \caption{Debug UART pin header connector on the PCB.}
        \label{fig:uart-pin-header}
    \end{center}
\end{figure}

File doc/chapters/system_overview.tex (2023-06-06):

%
% system_overview.tex
%
% Copyright The EPS 2.0 Contributors.
%
% EPS 2.0 Documentation
%
% This work is licensed under the Creative Commons Attribution-ShareAlike 4.0
% International License. To view a copy of this license,
% visit http://creativecommons.org/licenses/by-sa/4.0/.
%

%
% \brief System overview chapter.
%
% \author Gabriel Mariano Marcelino <gabriel.mm8@gmail.com>
% \author Yan Castro de Azeredo <yan.ufsceel@gmail.com>
%
% \version 0.3.0
%
% \date 2021/02/10
%

\chapter{System Overview} \label{ch:system-overview}

The board has a MSP430 low-power MCU\nomenclature{\textbf{MCU}}{\textit{Microcontroller.}} that runs the firmware application intended to control and communicate with its peripherals, subsystems, and other modules. The programming language used is C, and the firmware was developed using the Code Composer Studio IDE\nomenclature{\textbf{IDE}}{\textit{Integrated Development Environment.}} (a.k.a. CCS) for compiling, programming and testing. The module has many tasks, such as interfacing internal peripherals and communicating with other boards over distinct protocols and time requirements. 
So, in order to improve predictability, a Real-Time Operating System (RTOS\nomenclature{\textbf{RTOS}}{\textit{Real Time Operating System.}}) is used to ensure that the deadlines are observed, even under a fault situation in a routine. The RTOS chosen is the FreeRTOS (v10.2.1) since it is designed for embedded systems applications and was already validated in space applications. The firmware architecture follows an abstraction layer scheme to facilitate higher level implementations and allow more portability across different hardware platforms; see \autoref{sec:system-layers} for more details.

The EPS 2.0 is compatible with GOMspace Solar Panels or with panels of similar characteristics. Algorithms are implemented to improve power generation through MPPT. Also, the load output can be regulated through measurements to achieve a more efficient power distribution to the nanosatellite.

\section{Product tree}

The product tree of the EPS 2.0 module is available in \autoref{fig:product-tree}.

\begin{figure}[!ht]
    \begin{center}
        
        \caption{Product tree of the EPS 2.0 module.}
        \label{fig:product-tree}
    \end{center}
\end{figure}

\section{MCU Block Diagram}

The \autoref{fig:mcu-block-diagram} presents a simplified view of the module subsystems and interfaces through the microcontroller perspective. 
The MCU has a programming JTAG\nomenclature{\textbf{JTAG}}{\textit{Joint Test Action Group.}}, a dedicated UART\nomenclature{\textbf{UART}}{\textit{Universal Asynchronous Receiver/Transmitter.}} debug interface and 4 communication buses, divided in 4 different protocols (I2C\nomenclature{\textbf{I2C}}{\textit{Inter-Integrated Circuit.}}, SPI\nomenclature{\textbf{SPI}}{\textit{Serial Peripheral Interface.}} and UART). 

There is an I2C buffer to allow secure and proper communication with the OBDH 2.0 module \cite{obdh2}.
The SPI protocol is used for controlling and retrieving data from an additional ADC\nomenclature{\textbf{ADC}}{\textit{Analog-to-Digital Converter.}} IC that measures temperature sensors (RTDs\nomenclature{\textbf{RTD}}{\textit{Resistance Temperature Detector.}}) on the batteries board and solar panels.
Several parameters from the Batteries Management Subsystem are sent to the EPS 2.0 MCU via I2C protocol.
The UART bus that goes to the PC/104 is used for basic telemetry to be sent to the beacon microcontroller within the TTC module.
Besides these channels, there are GPIO\nomenclature{\textbf{GPIO}}{\textit{General Purpose Input/Output.}} connections for enabling and disabling power buses, for hard code PCB versioning, and some optional GPIOs that can be added and used though the PC/104 interface. 

The MCU reads the measurements of current and voltage of the solar panels from its ADC ports for the MPPT Subsystem; also, from these data, the MPPT is controlled by the microcontroller through PWM\nomenclature{\textbf{PWM}}{\textit{Pulse Width Modulation.}} signals.

An external charger is used to charge the batteries and kill-switches to power off the EPS 2.0 module during the test phase. Before launch, the kill-switches are also connected to the button switches present on a CubeSat structure.   

\begin{figure}[!ht]
    \begin{center}
        
        \caption{EPS 2.0 MCU Block diagram.}
        \label{fig:mcu-block-diagram}
    \end{center}
\end{figure}

\section{Power Block Diagram}

The \autoref{fig:power-block-diagram} presents a more detailed view of the power subsystems that complements the MCU Block Diagram. More details and descriptions about these hardware components and interfaces are provided in the \autoref{ch:hardware}.

\begin{figure}[!ht]
    \begin{center}
        
        \caption{EPS 2.0 Power Block diagram.}
        \label{fig:power-block-diagram}
    \end{center}
\end{figure}

\section{System Layers} \label{sec:system-layers}

The system is divided into various abstraction layers to favor high-level firmware implementations. The \autoref{fig:system-layers} shows this scheme, composed of third-party drivers at the lowest layer above the hardware, the operating system as the base building block of the module, the devices handling implementation, and the application tasks in the highest layer. More details are provided in the \autoref{ch:firmware}.

\begin{figure}[!ht]
    \begin{center}
        
        \caption{System layers.}
        \label{fig:system-layers}
    \end{center}
\end{figure}

\section{Operation} \label{sec:operation}

The system operates through the sequential execution of routines (tasks in the context of the operating system) that are scheduled and multiplexed through time. Each routine has a priority and a periodicity, determining the subsequent execution, the set of functionalities currently running, and the memory usage management.

Besides this deterministic scheduling system, the routines have communication channels with each other through the usage of queues, which provides a robust synchronization scheme. The system operation and internal nuances are described in detail in the \autoref{ch:firmware}. This section is a top view, user perspective, to describe the module's operation.

\subsection{Execution Flow}

To better understand how the EPS2 will operate during the mission, a simplified representation of its operation is presented in \autoref{fig:execution-flow}. Overall, the EPS2 should control the temperature of the battery and its energy harvesting system operation and obtain the sensors' measurements periodically. The OBDH or TTC modules can communicate with the EPS2, which should receive or transmit data as requested. Furthermore, every 10 hours, the EPS2 will reset.

\begin{figure}[!ht]
    \begin{center}
        
        \caption{Simplified representation of the EPS2'S execution flow.}
        \label{fig:execution-flow}
    \end{center}
\end{figure}

%\subsection{Data Flow}
% Add here a flowchart or diagram showing where and how the data is generated and transferred across different modules and peripherals.

\subsection{Status LEDs} \label{status-leds}

On the development version of the board, there are ten LED\nomenclature{\textbf{LED}}{\textit{Light-Emitting Diode.}}s that indicate some behaviors of the systems. This set of LEDs can be seen on \autoref{fig:status-leds}.

\begin{figure}[!ht]
    \begin{center}
        
        \caption{Available status LEDs.}
        \label{fig:status-leds}
    \end{center}
\end{figure}

A description of each of these LEDs is available below:

\begin{itemize}
    \item \textbf{6V\_RADIO\_1\_LED}: Indicates that the radio 1 transceiver 6V power is being sourced.
    \item \textbf{5V\_RADIO\_0\_LED}: Indicates that the radio 0 transceiver 5V power is being sourced.
    \item \textbf{SYSTEM\_ON}: Heartbeat of the system. It blinks at a frequency of 1 Hz when the system is running properly.
    \item \textbf{SYSTEM\_FAULT}: Indicates an error during the board's running firmware.
    \item \textbf{3V3\_ANT}: Indicates that the antenna deployer 3.3V power is being sourced.
    \item \textbf{3V3\_MCU}: Indicates that the EPS2 MCU 3.3V power is being sourced.
    \item \textbf{3V3\_OBDH}: Indicates that the OBDH module 3.3V power is being sourced.
    \item \textbf{3V3\_EPS\_BEACON}: Indicates that the EPS2 board and beacon MCU 3.3V power is being sourced.
    \item \textbf{5V\_PAYLOADS\_LEDS}: Indicates that the payloads 5V power is being sourced.
    \item \textbf{VBUS\_LED}: Indicates that the main power bus from the batteries is being sourced.
\end{itemize}

These LEDs are not mounted in the flight version of the module.

\section{Hard Code Versioning}

On the EPS2 board, there are 2 GPIOs dedicated to hard code versioning.
The on-board firmware can read these pins to identify the correct version of the hardware project.
Each line can be either pulled to VCC or ground, representing in binary as 1 and 0, respectively.
The \autoref{tab:versioning-resistors} shows the versioning representation up to the project's latest revision.

\begin{table}[!h]
    \centering
    \begin{tabular}{lcc}
        \toprule[1.5pt]
        \textbf{Version}    &   \textbf{P3.5 (pin code) / 47 (pin number)}    &    \textbf{P3.4 (pin code) / 46 (pin number)}\\
        \midrule
        v0.1                & 0                 & 0              \\
        v0.2                & 0                 & 1              \\
        v0.3                & 1                 & 0              \\        
        \bottomrule[1.5pt]
    \end{tabular}
    \caption{Hard code versioning table.}
    \label{tab:versioning-resistors}
\end{table}

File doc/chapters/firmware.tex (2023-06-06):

%
% firmware.tex
%
% Copyright The EPS 2.0 Contributors.
%
% EPS 2.0 Documentation
%
% This work is licensed under the Creative Commons Attribution-ShareAlike 4.0
% International License. To view a copy of this license,
% visit http://creativecommons.org/licenses/by-sa/4.0/.
%

%
% \brief Firmware project chapter.
%
% \author Gabriel Mariano Marcelino <gabriel.mm8@gmail.com>
% \author Yan Castro de Azeredo <yan.ufsceel@gmail.com>
%
% \version 0.3.0
%
% \date 2021/03/07
%

\chapter{Firmware} \label{ch:firmware}

\section{Product tree}

The product tree of the firmware part of the EPS 2.0 module is available in \autoref{fig:product-tree-fw}.

\begin{figure}[!ht]
    \begin{center}
        
        \caption{Product tree of the firmware of the EPS 2.0 module.}
        \label{fig:product-tree-fw}
    \end{center}
\end{figure}

%\section{Dependencies}

\section{Operating System}

The FreeRTOS 10 \cite{freertos} is being used as an operating system. FreeRTOS is a market-leading real-time operating system (RTOS) for microcontrollers and small microprocessors. Distributed freely under the MIT open-source license, FreeRTOS includes a kernel and a growing set of IoT libraries suitable for use across all industry sectors. FreeRTOS is built with an emphasis on reliability and ease of use.

The main configuration parameters of the operating system in this project are available in \autoref{tab:freertos-config}.

\begin{table}[!h]
    \centering
    \begin{tabular}{lrr}
        \toprule[1.5pt]
        \textbf{Parameter}       & \textbf{Value} & \textbf{Unit} \\
        \midrule
        Version                  & v10.2.0        & - \\
        Tick rate (Hz)           & 1000           & Hz \\
        CPU clock (HZ)           & 32             & MHz \\
        Max. priorities          & 5              & - \\
        Heap size                & 40690          & bytes \\
        Max. length of task name & 20             & - \\
        \bottomrule[1.5pt]
    \end{tabular}
    \caption{FreeRTOS main configuration parameters.}
    \label{tab:freertos-config}
\end{table}

More details of the used configuration parameters can be seen in the file \textit{\href{https://github.com/spacelab-ufsc/eps2/blob/master/firmware/config/FreeRTOSConfig.h}{firmware/config/FreeRTOSConfig.h}} from \cite{eps2}.

\section{Hardware Abstraction Layer (HAL)}

As the Hardware Abstraction Layer (HAL\nomenclature{\textbf{HAL}}{\textit{Hardware Abstraction Layer.}}), the DriverLib \cite{driverlib} from Texas Instruments is begin used. It is the official API to access the registers of the MSP430 microcontrollers.

The DriverLib is meant to provide a ``software'' layer to the programmer to facilitate higher level of programming than direct register accesses. By using the high level software APIs provided by DriverLib, users can create powerful and intuitive code that is highly portable between devices within the MSP430 platform and different families in the MSP430/MSP432 platforms.

\section{Tasks}

A list of the firmware tasks can be seen in the \autoref{tab:firmware-tasks}.

\begin{table}[!h]
    \centering
    \begin{tabular}{lccccc}
        \toprule[1.5pt]
        \textbf{name}          & \textbf{priority} & \textbf{initial delay [ms]} & \textbf{period [ms]} & \textbf{stack [bytes]} \\
        \midrule
        startup (boot)         & highest           & 0                           & aperiodic            & 500                    \\
        watchdog reset         & lowest            & 0                           & 100                  & 150                    \\
        heartbeat              & lowest            & 0                           & 500                  & 160                    \\
        system reset           & low               & 0                           & 36000000             & 128                    \\
        heater controller      & medium            & 0                           & 2000                  & 160                    \\
        read sensors           & low               & 0                           & 60000                & 512                    \\
       %csp server             & lowest            & 0                           & 500                  & 1024                   \\
        mppt                   & high              & 0                           & 300                  & 160                    \\
       %beacon package         & tbd               & tbd                         & tbd                  & tbd                    \\
       %obdh package           & highest           & 4500   & called by isr\nomenclature{\textbf{isr}}{\textit{interrupt service routine.}}   & tbd \\
        parameter server       & high              & 0      & called by isr\nomenclature{\textbf{isr}}{\textit{interrupt service routine.}}   & 300 \\
        time control           & high              & 0                           & 1000                 & 128                    \\
        \bottomrule[1.5pt]
    \end{tabular}
    \caption{Firmware tasks.}
    \label{tab:firmware-tasks}
\end{table}

\subsection{Startup (boot)}

This task is responsible for initializing all devices, drivers, libraries, and data structures upon system power-up or reboot.
It is the first task executed and unblocks the remaining tasks after the initialization is completed.

Task configuration parameters are shown in Table \ref{tab:firmware-tasks}.

\subsection{Watchdog reset}

This task is responsible for resetting the internal watchdog timer every \(100 ms\).
The internal watchdog timer has a \(1 s\) timeout.

This task has the lowest possible priority in order to prevent the watchdog from not triggering in case an anomaly happens in other tasks (longer than expected execution times, for example).

Task configuration parameters are shown in Table \ref{tab:firmware-tasks}.

\subsection{Heartbeat}

This task provides visual feedback indicating that the system is running correctly.
This feedback is given through blinking an LED ("SYSTEM\_ON" LED on Figure \ref{fig:status-leds}) at a frequency of \(1 Hz\), emulating a "heartbeat" for the system.

The usefulness of this task comes during the development of the engineering model of the module, providing information to the developers.
The flight model has no LEDs, so this task serves no purpose in that case. 

Task configuration parameters are shown in Table \ref{tab:firmware-tasks}.

\subsection{System reset}

This task is responsible for resetting the microcontroller via software every 10 hours.
This helps to clean up possible corrupted values in variables, retry a failed initialization, clean up RAM, etc.

Task configuration parameters are shown in Table \ref{tab:firmware-tasks}.

\subsection{Heater controller}

This task is responsible for monitoring and controlling the batteries' heaters.

The heaters and batteries' temperatures are monitored through a set of RTDs, read through an external ADC (\textit{ADS1248}), and activated through MOSFET drivers controlled by the MCUs GPIOs to prevent the batteries from operating below a critical temperature value.

This task has two modes of operation, automatic mode, and manual mode.

In automatic mode, the batteries' temperature readings occur every 2 seconds. The heaters' status is updated accordingly, based on the new reading and a predefined temperature limit, through the algorithm defined in the heater device.
This algorithm switches the heaters on or off based on the set temperature limits.

In manual mode, the heater is controlled manually through telecommands, independent of the temperature readings. In this mode, the heaters are controlled with a PWM signal with a duty cycle defined via telecommand.

Task configuration parameters are shown in Table \ref{tab:firmware-tasks}.

\subsection{Read sensors}

This task is responsible for reading all sensors available to the EPS 2.0 module and recording their values.
The readings occur every \(60 s\), and the results are written in the eps buffer data structure.

Task configuration parameters are shown in Table \ref{tab:firmware-tasks}.

\subsection{MPPT}

This task is responsible for running the MPPT algorithm for the solar panels to operate them at their maximum power point.
The algorithm itself is defined in the MPPT device.

The solar panels' current and voltage sensors are read every \(300 ms\), and the results are passed as inputs to the MPPT algorithm, which then controls the MPPT Boost circuit through a set o PWM outputs.

The MPPT task can also operate in manual mode, where the PWM outputs are set manually via telecommands.

Task configuration parameters are shown in Table \ref{tab:firmware-tasks}.

\subsection{Parameter Server}

This task is responsible for processing and responding to commands from the OBDH and TTC modules.

The commands are for reading and writing to the EPS buffer data structure, seen in \autoref{tab:eps2-variables}

Task configuration parameters are shown in Table \ref{tab:firmware-tasks}.

\subsection{Time Control}

This task is responsible for the time management of the system.
At every second, it increments the system time (epoch).
Also, it saves the current system time in the non-volatile memory at every minute.

Task configuration parameters are shown in Table \ref{tab:firmware-tasks}.

% \subsection{Beacon package}

% Task configuration parameters are shown in Table \ref{tab:firmware-tasks}.

% \subsection{OBDH package}

% Task configuration parameters are shown in Table \ref{tab:firmware-tasks}.

\section{Variables and Parameters}

A list of all the variables of EPS with their identification number (ID) and variable type that can be read from the sensors and peripherals is seen in the \autoref{tab:eps2-variables}.

\begin{longtable}[c]{cL{0.72\textwidth}lc}
    \toprule[1.5pt]
    \textbf{ID} & \textbf{Name/Description} & \textbf{Type} & \textbf{Access} \\
    \midrule
    0   & Time counter in milliseconds                                       & uint32 & R \\
    1   & Temperature of the $\mu$C in K                                    & uint16 & R \\
    2   & EPS circuitry current in mA                                       & uint16 & R \\
    \multirow{18}{*}{3} & Last reset cause: & \multirow{18}{*}{uint8} & \multirow{18}{*}{R} \\
        & - 0x00 = No interrupt pending                                     &        &  \\
        & - 0x02 = Brownout (BOR)                                           &        &  \\
        & - 0x04 = RST/NMI (BOR)                                            &        &  \\
        & - 0x06 = PMMSWBOR (BOR)                                           &        &  \\
        & - 0x08 = Wakeup from LPMx.5 (BOR)                                 &        &  \\
        & - 0x0A = Security violation (BOR)                                 &        &  \\
        & - 0x0C = SVSL (POR)                                               &        &  \\
        & - 0x0E = SVSH (POR)                                               &        &  \\
        & - 0x10 = SVML\_OVP (POR)                                          &        &  \\
        & - 0x12 = SVMH\_OVP (POR)                                          &        &  \\
        & - 0x14 = PMMSWPOR (POR)                                           &        &  \\
        & - 0x16 = WDT time out (PUC)                                       &        &  \\
        & - 0x18 = WDT password violation (PUC)                             &        &  \\
        & - 0x1A = Flash password violation (PUC)                           &        &  \\
        & - 0x1C = Reserved                                                 &        &  \\
        & - 0x1E = PERF peripheral/configuration area fetch (PUC)           &        &  \\
        & - 0x20 = PMM password violation (PUC)                             &        &  \\
        & - 0x22 to 0x3E = Reserved                                         &        &  \\
    4   & Reset counter                                                     & uint16 & R \\
    5   & -Y and +X sides solar panel voltage in mV                         & uint16 & R \\
    6   & -X and +Z sides solar panel voltage in mV                         & uint16 & R \\
    7   & -Z and +Y sides solar panel voltage in mV                         & uint16 & R \\
    8   & -Y side solar panel current in mA                                 & uint16 & R \\
    9   & +Y side solar panel current in mA                                 & uint16 & R \\
    10  & -X side solar panel current in mA                                 & uint16 & R \\
    11  & +X side solar panel current in mA                                 & uint16 & R \\
    12  & -Z side solar panel current in mA                                 & uint16 & R \\
    13  & +Z side solar panel current in mA                                 & uint16 & R \\
    14  & MPPT 1 duty cycle in \% (writable just in manual mode)            & uint8  & R/W \\
    15  & MPPT 2 duty cycle in \% (writable just in manual mode)            & uint8  & R/W \\
    16  & MPPT 3 duty cycle in \% (writable just in manual mode)            & uint8  & R/W \\
    17  & Total solar panels output voltage after MPPT in mV                & uint16 & R \\
    18  & Main power bus voltage in mV                                      & uint16 & R \\
    19  & RTD0 temperature in K                                             & uint16 & R \\
    20  & RTD1 temperature in K                                             & uint16 & R \\
    21  & RTD2 temperature in K                                             & uint16 & R \\
    22  & RTD3 temperature in K                                             & uint16 & R \\
    23  & RTD4 temperature in K                                             & uint16 & R \\
    24  & RTD5 temperature in K                                             & uint16 & R \\
    25  & RTD6 temperature in K                                             & uint16 & R \\
    26  & Batteries voltage in mV                                           & uint16 & R \\
    27  & Batteries current in mA                                           & uint16 & R \\
    28  & Batteries average current in mA                                   & uint16 & R \\
    29  & Batteries accumulated current in mA                               & uint16 & R \\
    30  & Batteries charge in mAh                                           & uint16 & R \\
    31  & Battery monitor IC temperature in K                               & uint16 & R \\
    32  & Battery monitor status register                                   & uint8  & R \\
    33  & Battery monitor protection register                               & uint8  & R \\
    34  & Battery monitor cycle counter                                     & uint8  & R \\
    35  & Battery monitor Remaining Active-Absolute Capacity (RAAC) in mAh  & uint16 & R \\
    36  & Battery monitor Remaining Standby-Absolute Capacity (RSAC) in mAh & uint16 & R \\
    37  & Battery monitor Remaining Active-Relative Capacity (RARC) in \%   & uint8  & R \\
    38  & Battery monitor Remaining Standby-Relative Capacity (RSRC) in \%  & uint8  & R \\
    39  & Battery heater 1 duty cycle in \% (writable just in manual mode)  & uint8  & R/W \\
    40  & Battery heater 2 duty cycle in \% (writable just in manual mode)  & uint8  & R/W \\
    41  & Hardware version                                                  & uint8  & R \\
    42  & Firmware version (ex.: ``v1.2.3''' = 0x00010203)                  & uint32 & R \\
    43  & MPPT 1 mode (0x00 = automatic, 0x01 = manual)                     & uint8  & R/W \\
    44  & MPPT 2 mode (0x00 = automatic, 0x01 = manual)                     & uint8  & R/W \\
    45  & MPPT 3 mode (0x00 = automatic, 0x01 = manual)                     & uint8  & R/W \\
    46  & Battery heater 1 mode (0x00 = automatic, 0x01 = manual)           & uint8  & R/W \\
    47  & Battery heater 2 mode (0x00 = automatic, 0x01 = manual)           & uint8  & R/W \\
    48  & Device ID (0xEEE2)                                                & uint16 & R \\
    \bottomrule[1.5pt]
    \caption{Variables and parameters of the EPS 2.0.}
    \label{tab:eps2-variables}
\end{longtable}

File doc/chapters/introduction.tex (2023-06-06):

%
% introduction.tex
%
% Copyright (C) 2021 by SpaceLab.
%
% EPS 2.0 Documentation
%
% This work is licensed under the Creative Commons Attribution-ShareAlike 4.0
% International License. To view a copy of this license,
% visit http://creativecommons.org/licenses/by-sa/4.0/.
%

%
% \brief Introduction chapter.
%
% \author Gabriel Mariano Marcelino <gabriel.mm8@gmail.com>
% \author Yan Castro de Azeredo <yan.ufsceel@gmail.com>
%
% \institution Universidade Federal de Santa Catarina (UFSC)
%
% \version 0.2.0
%
% \date 2021/03/16
%

\chapter{Introduction} \label{ch:introduction}

The EPS 2.0\nomenclature{\textbf{EPS}}{\textit{Electric Power System.}} is a PCB\nomenclature{\textbf{PCB}}{\textit{Printed Circuit Board.}} designed to harvest, store and distribute energy for a nanosatellite. It is one of the service modules developed for FloripaSat-2 CubeSat Mission \cite{floripasat2-doc}. The energy harvesting system is based on solar energy conversion through ten solar panels attached to the 2U CubeSat structure. The EPS 2.0 is designed to operate the solar panels at their maximum power point (MPPT)\nomenclature{\textbf{MPPT}}{\textit{Maximum Power Point Tracking.}}. The board is also responsible for measuring solar panels current, voltage, and temperature of both the panels and the batteries. The harvested solar energy is stored in the Battery Module 4C \cite{bat4c} connected to the EPS. Several integrated buck DC-DC converters do the energy distribution. The total EPS system comprises solar panels, the EPS 2.0 PCB, and the battery module. A general view of the EPS 2.0 board can be seen in \autoref{fig:general-view}.

The module is a direct upgrade from the EPS of FloripaSat-1 \cite{eps-fsat}, which grants a flight heritage rating. The improvements focus on providing a cleaner and more generic implementation compared to the previous version, more reliability in software, and adaptations for the new mission requirements. All the project (source and documentation files) is available freely on a GitHub repository \cite{eps2} under its respective licenses.

\begin{figure}[!ht]
    \begin{center}
        
        \caption{3D view of the EPS 2.0 PCB.}
        \label{fig:general-view}
    \end{center}
\end{figure}

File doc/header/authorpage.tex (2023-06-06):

%
% authorpage.tex
%
% Copyright The EPS 2.0 Contributors.
%
% EPS 2.0 Documentation
%
% This work is licensed under the Creative Commons Attribution-ShareAlike 4.0
% International License. To view a copy of this license,
% visit http://creativecommons.org/licenses/by-sa/4.0/.
%

%
% \brief Author page.
%
% \author Gabriel Mariano Marcelino <gabriel.mm8@gmail.com>
% \author Yan Castro de Azeredo <yan.ufsceel@gmail.com>
%
% \version 0.3.0
%
% \date 2021/06/07
%

\thispagestyle{empty}

\begin{center}

\textbf{\thetitle}

\textit{April, 2023}

\vspace{1cm}

\textbf{Project Chief:}

Eduardo Augusto Bezerra <\href{mailto:eduardo.bezerra@spacelab.ufsc.br}{eduardo.bezerra@spacelab.ufsc.br}>

\vspace{1cm}

\textbf{Authors:}

André Martins Pio de Mattos <\href{mailto:andre.mattos@spacelab.ufsc.br}{andre.mattos@spacelab.ufsc.br}>\\
Gabriel Mariano Marcelino <\href{mailto:gabriel.marcelino@spacelab.ufsc.br}{gabriel.marcelino@spacelab.ufsc.br}>\\
Yan Castro de Azeredo <\href{mailto:yan.azeredo@spacelab.ufsc.br}{yan.azeredo@spacelab.ufsc.br}>\\
João Cláudio Elsen Barcellos <\href{mailto:joao.claudio.barcellos@spacelab.ufsc.br}{joao.claudio.barcellos@spacelab.ufsc.br}>\\
Ramon de Araujo Borba \\
Augusto Cezar Boldori Vassoler \\ 
Vinicius Pimenta Bernardo \\

\vspace{1cm}

\textbf{Contributing Authors:}

Leonardo Kessler Slongo \\
Sara Vega Martinez \\
Bruno Vale Barbosa Eiterer \\
Túlio Gomes Pereira \\

\vspace{1cm}

\textbf{Revision Control:}

\end{center}

\begin{table}[!ht]
    \begin{center}
        \begin{tabular}{cL{5cm}L{5.5cm}C{2cm}}
            \toprule[1.5pt]
            \textbf{Version} & \textbf{Author}  & \textbf{Changes}    & \textbf{Date} \\
            \midrule
            0.1     & G. Marcelino              & Document creation   & 2020/11 \\ %/05
            0.2     & Y. C. Azeredo, G. Marcelino & First stable hardware & 2021/06 \\ %/28
            0.3     & G. Marcelino, J.C.E. Barcellos, R.A. Borba & Adding task sections and updating the tests and hardware sections & 2022/11        \\
            0.4     & J.C.E. Barcellos, R.A. Borba & Text refactoring, general improvements & 2023/04   \\
            \bottomrule[1.5pt]
        \end{tabular}
    \end{center}
\end{table}

\vfill

\begin{figure}[!h]
	\begin{center}
		
	\end{center}
\end{figure}

\textcopyright\  2023 by SpaceLab. \thetitle. This work is licensed under the Creative Commons Attribution-ShareAlike 4.0 International License. To view a copy of this license, visit \href{http://creativecommons.org/licenses/by-sa/4.0/}{http://creativecommons.org/licenses/by-sa/4.0/}.

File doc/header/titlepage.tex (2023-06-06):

%
% titlepage.tex
%
% Copyright The EPS 2.0 Contributors.
%
% EPS 2.0 Documentation
%
% This work is licensed under the Creative Commons Attribution-ShareAlike 4.0
% International License. To view a copy of this license,
% visit http://creativecommons.org/licenses/by-sa/4.0/.
%

%
% \brief Title page.
%
% \author Gabriel Mariano Marcelino <gabriel.mm8@gmail.com>
% \author Yan Castro de Azeredo <yan.ufsceel@gmail.com>
%
% \version 0.3.0
%
% \date 2020/06/07
%

\begin{titlepage}

\thispagestyle{empty}

\begin{flushleft}
SLB-EPS2-DOC-v0.4
\end{flushleft}

\vspace{1cm}

\begin{figure}[!ht]
    \begin{flushleft}
        
    \end{flushleft}
\end{figure}

\begin{flushleft}
\Huge{\textbf{\thetitle}}
\rule[0pt]{\textwidth}{5pt}
\end{flushleft}

\vspace{0.2cm}

\begin{flushleft}
\textit{\thetitle} \\
\textit{SpaceLab, Universidade Federal de Santa Catarina, Florianópolis - Brazil}
\end{flushleft}

\vfill
\vfill

\begin{flushright}
April, 2023
\end{flushright}

\end{titlepage}

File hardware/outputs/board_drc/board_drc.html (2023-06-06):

Altium

# Design Rule Verification Report

Date: | | 02/05/2023
Time: | | 19:44:15
Elapsed Time: | | 00:00:01
Filename: | | C:\Users\joaoc\Documents\eps2\hardware\sources\board_layout.pcbdoc

Warnings: | | 0
Rule Violations: | | 0

## Summary

Warnings | Count
Total | 0

Rule Violations | Count
Clearance Constraint (Gap=0.178mm) (InNet('DGND')),(All) | 0
Clearance Constraint (Gap=0mm) (InNet('+RBF')),(InNet('+RBF')) | 0
Clearance Constraint (Gap=0.178mm) (InNet('AGND')),(InNet('AGND')) | 0
Clearance Constraint (Gap=0mm) (InNet('VPANELS')),(InNet('VPANELS')) | 0
Clearance Constraint (Gap=0mm) (InNet('Net7_1')),(InNet('Net7_1')) | 0
Clearance Constraint (Gap=0mm) (InNet('-VBAT')),(InNet('-VBAT')) | 0
Clearance Constraint (Gap=0.254mm) (InNet('PGND')),(All) | 0
Clearance Constraint (Gap=0.381mm) (InNet('DGND')),(InNet('AGND')) | 0
Clearance Constraint (Gap=0.178mm) (All),(All) | 0
Short-Circuit Constraint (Allowed=No) (All),(All) | 0
Un-Routed Net Constraint ( (All) ) | 0
Width Constraint (Min=0.127mm) (Max=1.778mm) (Preferred=0.381mm) (All) | 0
Power Plane Connect Rule(Direct Connect )(Expansion=0.508mm) (Conductor Width=0.254mm) (Air Gap=0.254mm) (Entries=4) (InNetClass('power')) | 0
Power Plane Connect Rule(Relief Connect )(Expansion=0.508mm) (Conductor Width=0.254mm) (Air Gap=0.254mm) (Entries=4) (All) | 0
Hole Size Constraint (Min=0.025mm) (Max=5.08mm) (All) | 0
Hole To Hole Clearance (Gap=0.254mm) (All),(All) | 0
Minimum Solder Mask Sliver (Gap=0mm) (All),(All) | 0
Silk To Solder Mask (Clearance=0mm) (IsPad),(All) | 0
Silk to Silk (Clearance=0.127mm) (All),(All) | 0
Net Antennae (Tolerance=0mm) (All) | 0
Height Constraint (Min=0mm) (Max=1790.783mm) (Prefered=12.7mm) ('PCB_Project_Batteries') | 0
Total | 0

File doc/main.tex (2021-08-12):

%
% main.tex
%
% Copyright (C) 2021 by SpaceLab.
%
% EPS 2.0 Documentation
%
% This work is licensed under the Creative Commons Attribution-ShareAlike 4.0
% International License. To view a copy of this license,
% visit http://creativecommons.org/licenses/by-sa/4.0/.
%

%
% \brief Main file.
%
% \author Gabriel Mariano Marcelino <gabriel.mm8@gmail.com>
%
% \institution Universidade Federal de Santa Catarina (UFSC)
%
% \version 0.2.0
%
% \date 2020/11/05
%

\documentclass[a4paper,12pt]{book}

\usepackage{spacelab_book}

\title{EPS 2.0 Documentation}
\author{SpaceLab}
\date{\today}

% File metadata
\hypersetup
{
    pdfauthor   = {SpaceLab},
    pdfsubject  = {\thetitle},
    pdftitle    = {\thetitle},
    pdfkeywords = {Nanosatellites, CubeSats, Electric Power System}
}

\begin{document}

    \pagenumbering{roman}
    \setcounter{page}{1}

    \input{header/titlepage}
    \cleardoublepage
    \input{header/authorpage}
    \cleardoublepage

    \listoffigures
    \addcontentsline{toc}{chapter}{List of Figures}

    \listoftables
    \addcontentsline{toc}{chapter}{List of Tables}

    \printnomenclature
    \addcontentsline{toc}{chapter}{Nomenclature}

    \tableofcontents
    \cleardoublepage
    
    \pagenumbering{arabic}
    \setcounter{page}{1}

    \input{chapters/introduction}
    \input{chapters/system_overview}
    \input{chapters/hardware}
    \input{chapters/firmware}
    \input{chapters/assembly}
    \input{chapters/instructions}
    \input{chapters/tests}
    \input{chapters/references}
    \input{appendices/appendices}

\end{document}

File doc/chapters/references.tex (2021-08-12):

%
% references.tex
%
% Copyright (C) 2021 by SpaceLab.
%
% EPS 2.0 Documentation
%
% This work is licensed under the Creative Commons Attribution-ShareAlike 4.0
% International License. To view a copy of this license,
% visit http://creativecommons.org/licenses/by-sa/4.0/.
%

%
% \brief References chapter.
%
% \author Gabriel Mariano Marcelino <gabriel.mm8@gmail.com>
% \author Yan Castro de Azeredo <yan.ufsceel@gmail.com>
%
% \institution Universidade Federal de Santa Catarina (UFSC)
%
% \version 0.2.0
%
% \date 2021/03/16
%

\bibliography{references/floripasat2-doc,%
			references/bat4c,%
			references/eps-fsat,%
			references/eps2,%
			references/obdh2,%
			references/msp430f6659,%
			references/iip,%
			references/driverlib,%
			references/freertos}

\addcontentsline{toc}{chapter}{References}

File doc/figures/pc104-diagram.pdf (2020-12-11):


1-2 3-4 5-6 7-8 9-10 11-12 13-14 15-16 17-18 19-20 21-22 23-24 25-26 27-28 29-30 31-32 33-34 35-36 37-38 39-40 41-42 43-44 45-46 47-48 49-50 51-52 | 1-2 3-4 5-6 7-8 9-10 11-12 13-14 15-16 17-18 19-20 21-22 23-24 25-26 27-28 29-30 31-32 33-34 35-36 37-38 39-40 41-42 43-44 45-46 47-48 49-50 51-52 H1-H2 H1-50 | H2-51

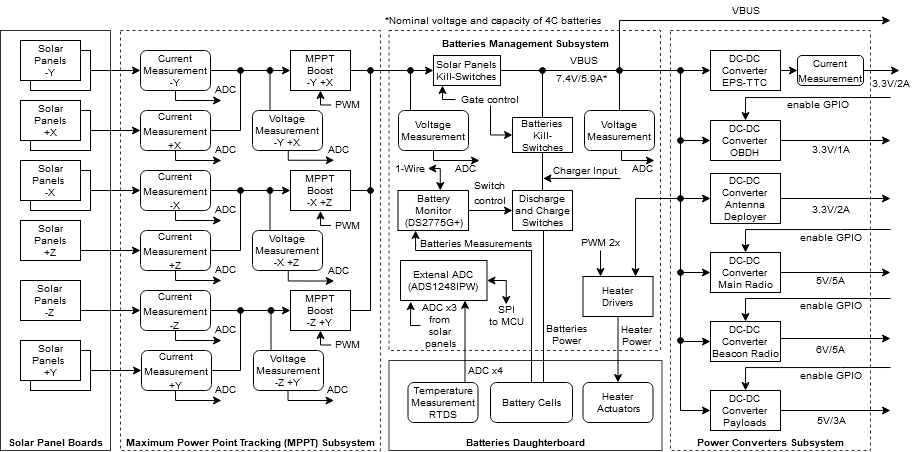
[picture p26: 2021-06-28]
hardware/images/eps2_power_diagram.png

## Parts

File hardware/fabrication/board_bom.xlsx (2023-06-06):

Comment | Description | Quantity | Designator | Fitted | Partnumber | Footprint | Manufacturer | Manufacturer Part Number | Mount
0.1uF/50V | CAP CER 0.1UF 50V 10% X7R 0603 | 44 | C40, C41, C58, C59, C63, C71, C72, C73, C74, C75, C76, C83, C84, C85, C86, C87, C88, C89, C90, C91, C93, C94, C97, C98, C99, C100, C101, C108, C109, C110, C111, C112, C113, C114, C115, C116, C119, C120, C121, C122, C124, C128, C129, C133 | Fitted | CC0603KPX7R9BB104 | CC0603 | Yageo | CC0603KPX7R9BB104 | Surface Mount
0.1uF/50V | CAP CER 0.1UF 50V 10% X7R 0805 | 19 | C1, C2, C5, C11, C12, C15, C22, C25, C27, C29, C45, C47, C53, C55, C62, C77, C78, C126, C127 | Fitted | CC0805KRX7R9BB104 | CC0805 | Yageo | CC0805KRX7R9BB104 | Surface Mount
0R | RES 0.0 OHM 3/4W JUMP 1206 | 15 | R2, R3, R9, R10, R15, R16, R20, R21, R46, R47, R50, R51, R55, R56, R93 | Fitted | HCJ1206ZT0R00 | 1206 | Stackpole Electronics | HCJ1206ZT0R00 | Surface Mount
1k | RES 1.0K OHM 1/8W 1% 0603 | 15 | R1, R8, R18, R23, R31, R34, R37, R39, R40, R43, R53, R58, R60, R61, R80 | Fitted | MCT06030C1001FP500 | 0603, R0603 | Vishay | MCT06030C1001FP500 | Surface Mount
0R | RES 0R OHM 1/8W JUMPER 0805 | 12 | J_V1, J_V3, J_V4, J_V5, J_V6, R28, R32, R87, R88, R89, R90, R91 | Fitted | CRCW08050000Z0EA | 0805 | Vishay | CRCW08050000Z0EA
4.7uF/25V | CAP CER 4.7uF 25V 10% X7R 0805 | 11 | C3, C4, C13, C14, C102, C103, C104, C105, C106, C107, C130 | Fitted | CC0805KKX7R8BB475 | CC0805 | Yageo | CC0805KKX7R8BB475 | Surface Mount
22uF/10V | CAP CER 22uF 10V 10% X7R 1206 | 10 | C6, C7, C8, C16, C17, C18, C30, C48, C131, C132 | Fitted | GRM31CR71A226KE15L | CC1206 | Murata | GRM31CR71A226KE15L | Surface Mount
22uF/25V | CAP CER 22uF 25V 10% X7R 1210 | 9 | C36, C50, C51, C79, C80, C81, C82, C117, C118 | Fitted | GRM32ER71E226KE15L | CC1210 | Murata | GRM32ER71E226KE15L | Surface Mount
DNP | SMD Green LED | 8 | 3V3_ANT, 3V3_EPS_BEACON, 3V3_MCU, 3V3_OBDH, 5V_PAYLOADS_LED, 5V_RADIO_0_LED, 6V_RADIO_1_LED, VBUS_LED | Fitted | 150060VS75000 | 0603-LED | Wurth Electronics | 150060VS75000 | Surface Mount
10uF/10V | CAP Tantalum 10uF 6.3V 10% 0805 | 7 | C33, C35, C60, C61, C64, C123, C125 | Fitted | TPSR106K006R1000 | CC0805_Tantalum | Kyocera AVX | TPSR106K006R1000 | Surface Mount
Header 4_PicoBlade, 0533980471 | Header, 4-Pin, PicoBlade 4 Position Vertical Connector Header Surface Mount 0.049" (1.25mm) | 7 | +X, +Y, +Z, RBF, -X, -Y, -Z | Fitted | 53398-0471 | HDR4 PicoBlade, PICOBLADE 4PIN VERTICAL | Molex | 53398-0471 | Surface Mount
MAX9934TAUA+ | MAX9934TAUA+ | 7 | U15, U16, U18, U20, U22, U25, U27 | Fitted | MAX9934TAUA+ | MSOP-8 | Maxim | MAX9934TAUA+
0.01uF/50V | CAP CER 0.01uF 50V 10% X7R 0805 | 6 | C21, C26, C32, C34, C44, C52 | Fitted | 08055C103KAT4A | CC0805 | Kyocera AVX | 08055C103KAT4A | Surface Mount
0.02R/0.5W | Current Sense Resistors - SMD 0.02ohm .5% 4 Terminal | 6 | R29, R41, R49, R68, R75, R78 | Fitted | LVK12R020DER | 1206 - ohmite | Ohmite | LVK12R020DER | Surface Mount
3k3 | RES SMD 3.3K OHM 0.1% 1/10W 0805 | 6 | R30, R48, R67, R72, R77, R79 | Fitted |  | R0805 | TE Connectivity Neohm | CPF0805B3K3E1 | Surface Mount
DNP | Diode Schottky 20 V 2A Surface Mount SOD-323 | 6 | D7, D12, D14, D16, D17, D18 | Fitted | SMD22WS-TP | SOD323F
100K | RES 100K OHM 1/10W 1% 0603 | 5 | R71, R73, R76, R82, R86 | Fitted | CRCW0603100KFKEA | 0603 | Vishay | CRCW0603-100KFKEA
B340LA-13-F | DIODE SCHOTTKY 40V 3A B340LA-13-F | 5 | D4, D9, D11, D13, D15 | Fitted | B340LA-13-F | DO-214AC | Diodes | B340LA-13-F | Surface Mount
MOSFET-N | MOSFET N-Channel 30V Vds 20V Vgs SO-8 | 5 | Q1, Q2, Q8, Q9, Q10 | Fitted | SI4166DY-T1-GE3 | SOIC8_Mosfet | Vishay Siliconix | SI4166DY-T1-GE3 | Surface Mount
TLV341AIDBVR | TLV341AIDBVR | 5 | U17, U19, U21, U24, U26 | Fitted | TLV341AIDBVR | SOT-23 6L | Texas Instruments | TLV341AIDBVR
10k | RES 10K OHM 1/8W 1% 0603 | 4 | R65, R66, R83, R84 | Fitted | MCT0603MC1002FP500 | R0603 | Vishay Beyschlag | MCT0603MC1002FP500
10k | RES 10K OHM 1/8W 1% 0805 | 4 | R17, R22, R52, R57 | Fitted | CRCW080510K0FKEA | 0805 | Vishay | CRCW080510K0FKEA
10uF/25V | CAP CER 10uF 25V 10% X7R 1206 | 4 | C23, C28, C46, C54 | Fitted | GRM31CR71E106KA12L | CC1206 | Murata | GRM31CR71E106KA12L | Surface Mount
47k, DNP | RES 47k OHM 1/10W 1% 0805 | 4 | V1, V2, V3, V4 | Fitted | RC0805FR-0747KL | 0805
150R | RES 150R OHM 1/10W 1% 0603 | 4 | R33, R42, R44, R92 | Fitted | CRCW0603150RFKEA | 0603, R0603 | Vishay | CRCW0603150RFKEA | Surface Mount
220uF/6.3V | CAP Tantalum 220uF 6.3V 20% 1210 | 4 | C24, C31, C49, C56 | Fitted | 6TPE220MAZB | cc1210 | Panasonic | 6TPE220MAZB | Surface Mount
MOSFET-P-SI4403CDY-T1-GE3 | MOSFET 1.8V P-Channel 20 V, 0.0155 Ω typ., 13.4 A | 4 | Q3, Q4, Q5, Q6 | Fitted | SI4403CDY-T1-GE3 | SOIC8_Mosfet | Vishay Siliconix | SI4403CDY-T1-GE3 | Surface Mount
5K9 | RES 5K9 OHM 1/8W 1% 0805 | 3 | R19, R24, R54 | Fitted | 71-CRCW0805-5.9K-E3 | 0805 | Vishay | CRCW08055K90FKEA
93K1 | RES 93.1K OHM 1/10W 1% 0603 | 3 | R69, R74, R81 | Fitted | CRCW060393K1FKEA | 0603 | Vishay | CRCW060393K1FKEA | Surface Mount
100uH/2.2/150.2mOHM | MSS1278T-104MLD - 100uH / 2.2A / 150.2mOHM | 3 | L7, L8, L9 | Fitted |  | IND_HC9
0532610671 | PicoBlade 6 Position Right Angle Connector Header Surface Mount 0.049" (1.25mm) | 3 | SBW, SW1, SW2 | Fitted | 53398-0671 | PICOBLADE 6PIN Right Angle
0532610871 | PicoBlade 8 Position Right Angle Connector Header Surface Mount 0.049" (1.25mm) | 3 | P8, RTD1, RTD2 | Fitted | 53261-0871 | PICOBLADE 8PIN RIGHT ANGLE | Molex | 53261-0871 | Surface Mount
0.47uF/50V | CAP CER 0.47UF 50V 10% X7R 0603 | 2 | C39, C65 | Fitted | C1608X7R1H474K080AE | CC0603 | TDK | C1608X7R1H474K080AE | Surface Mount
1k | RES SMD 1K OHM 1% 1/8W 0805 | 2 | R25, R26 | Fitted |  | 0805 | Panasonic | ERJ-6ENF1001V | Surface Mount
2.2uH/9A 15mOHM | INDUCTOR 2.2UH 9A SMD | 2 | L1, L2 | Fitted | SRP6540-2R2M | Ind_SRP6540 | Bourns | SRP6540-2R2M | Surface Mount
3SMAJ5919B-TP, DNP | DIODE ZENER 5.6V 3W DO214AC | 2 | D5, D6 | Fitted | 3SMAJ5919B-TP | DO-214AC | MCC | 3SMAJ5919B-TP | Surface Mount
5.6nF/100V | CAP CER 5.6nF 100V 0603 | 2 | C10, C20 | Fitted | C1608C0G2A562J080AE | CC0603 | TDK | C1608C0G2A562J080AE
10pF/100V | CAP CER 10pF 100V 0805 | 2 | C68, C70 | Fitted | 08051A100FAT2A | CC0805 | Kyocera AVX | 08051A100FAT2A | Surface Mount
11.5k | RES 11.5k OHM 1/8W 1% 0805 | 2 | R6, R13 | Fitted | AC0805FR-0711K5L | 0805 | Yageo | AC0805FR-0711K5L
12pF/50V | CAP CER 12pF 50V 0603 | 2 | C67, C69 | Fitted | GQM1885C1H120GB01D | CC0603 | Murata | GQM1885C1H120GB01D | Surface Mount
13pF/50V | CAP CER 13PF 50V 0603 NP0 | 2 | C9, C19 | Fitted | C0603C130J5GAC7867 | CC0603 | KEMET | C0603C130J5GACTU | Surface Mount
16uH/5A/34.5mOHM | INDUCTOR 16UH 5A SMD | 2 | L4, L5 | Fitted | 7443251600 | IND_744325xxx | Wurth Electronics | 7443251600 | Surface Mount
19.6k | RES 19.6k OHM 1/10W 1% 0603 | 2 | R5, R12 | Fitted | ERJ-3EKF1962V | 0603 | Panasonic | ERJ-3EKF1962V | Surface Mount
30R@100Mhz, 10A | Ferrite Bead 30 OHM 10A 100MHz | 2 | FB3, FB4 | Fitted | BLE32PN300SN1L | IND1210 | Murata | BLE32PN300SN1L | Surface Mount
100K 1/10W | RES 100K OHM 1/10W 0.1% 0805 | 2 | R35, R85 | Fitted | CPF-A-0805B100KE | 0805 | TE Connectivity | CPF-A-0805B100KE
140k | RES 140k OHM 1/5W 1% 0603 | 2 | R7, R14 | Fitted | ERJ-P03F1403V | 0603 | Panasonic | ERJ-P03F1403V | Surface Mount
300K | RES 300K OHM 1/10W 0.1% 0603 | 2 | R45, R70 | Fitted | RG1608P-304-B-T5 | 0603 | Susumu | RG1608P-304-B-T5
1000pF/50V | CAP CER 1000pF 50V 10% X7R 0603 | 2 | C37, C38 | Fitted | CC0603KRX7R9BB102 | CC0603 | Yageo | CC0603KRX7R9BB102 | Surface Mount
FSV530AF | DIODE SCHOTTKY 30V 5A DO-214AA | 2 | D1, D2 | Fitted | FSV530AF | DO-214AC | ON Semiconductor / Fairchild | FSV530AF | Surface Mount
Header 5X2IPS1-105-01-S-D | 10 Position Receptacle Connector 0.100" (2.54mm) | 2 | P1, P5 | Fitted | IPS1-105-01-S-D | IPS1-105-01-S-D | Samtec | IPS1-105-01-S-D | Through Hole
TPS5420QDRQ1 | TPS5420QDRQ1 | 2 | U4, U9 | Fitted | TPS5420QDRQ1 | SO8 Power PAD | Texas Instruments | TPS5420QDRQ1 | Surface Mount
TPS54540QDDARQ1 | TPS54540QDDARQ1 | 2 | U2, U14 | Fitted | TPS54540QDDARQ1 | SO8 Power PAD | Texas Instruments | TPS54540QDDARQ1 | Surface Mount
0.01R/0.5W | Current Sense Resistors - SMD 0.01ohm .5% 4 Terminal | 1 | RSense1 | Fitted | LVK12R010DER | 1206 - ohmite | Ohmite | LVK12R010DER | Surface Mount
0.01uF/25V | CAP CER 0.01UF 25V 5% X7R 0603 | 1 | C66 | Fitted | 06033C103JAT4A | CC0603 | Kyocera AVX | 06033C103JAT4A | Surface Mount
0.075R/0.5W | Current Sense Resistors - SMD 1/2W 0.075 OHMS 1% 4 Terminal | 1 | Rsense3 | Fitted | LVK12R075FER | 1206 - ohmite | Ohmite | LVK12R075FER
1nF/16V | CAP CER 1nF 16V 0603 5% | 1 | C57 | Fitted | C0603X102J4RECAUTO | CC0805 | KEMET | C0603X102J4RECAUTO | Surface Mount
1.2M | RES 1200K OHM 1/8W 0.1% 0805 | 1 | R_ESD | Fitted | RG2012P-125-B-T5 | 0805 | Susumu | RG2012P-125-B-T5
1.65K | RES 1.65K OHM 1/10W 0.1% 0805 | 1 | R27 | Fitted | PCF0805R-1K65BT1 | 0805 | TT Welwyn | PCF0805R-1K65BT1
3.24k 1/8W | RES 3.24k OHM 1/8W 1% 0805 SMD | 1 | R59 | Fitted | CRCW08053K24FKEA | 0805 | Vishay | CRCW08053K24FKEA
4K7 | RES 4K7 OHM 1/8W 1% 0603 | 1 | R64 | Fitted | MCT06030C4701FP500 | 0603 | Vishay Beyschlag | MCT06030C4701FP500 | Surface Mount
4.02k | RES 4.02k OHM 1/8W 0.1% 0805 | 1 | R36 | Fitted | ERA-6AEB4021V | 0805 | Panasonic | ERA-6AEB4021V | Surface Mount
10uH/6.4A/51.8mOHM | INDUCTOR 2.2UH 6.4A SMD | 1 | L6 | Fitted | IHLP3232DZER100M11 | Ind_IHLP | Vishay Dale | IHLP3232DZER100M11 | Surface Mount
27uH/4.3A/42.5mOHM | INDUCTOR 27UH 4.3A SMD | 1 | L3 | Fitted | 7447798271 | IND_744325xxx | Wurth Electronics | 7447798271 | Surface Mount
30R@100Mhz, 3A | Ferrite Bead 30 OHM 3A 100MHz | 1 | FB1 | Fitted | BLM21PG300SN1D | IND0805 | Murata | BLM21PG300SN1D
32MHz 10ppm | 32MHz ±10ppm Crystal 10pF 60 Ohm -40°C ~ 125°C | 1 | Y1 | Fitted | ABM8X-102-32.000MHZ-T | XTAL_ABM8X | Abracon | ABM8X-102-32.000MHZ-T | Surface Mount
32.768kHz 12.5pF | 32.768kHz ±20ppm Crystal 12.5pF 70 kOhm -40°C ~ 125°C | 1 | Y2 | Fitted | ECS-.327-12.5-34S-TR | ABS06 0805 | ECS International | ECS-.327-12.5-34S-TR | Surface Mount
47k | RES 47K OHM 1/8W 0.5% 0603 | 1 | R62 | Fitted | MCT0603MD4702DP500 | 0603 | Vishay | MCT0603MD4702DP500
60.4k | RES 60.4k OHM 1/8W 1% 0805 | 1 | R11 | Fitted | ERJ-6ENF6042V | 0805 | Panasonic | ERJ-6ENF6042V | Surface Mount
75k | RES 75k OHM 1/8W 1% 0805 | 1 | R4 | Fitted | RMCF0805FT75K0 | 0805 | Panasonic | RMCF0805FT75K0 | Surface Mount
470R | RES 470R OHM 1/8W 1% 0603 | 1 | R38 | Fitted | MCT06030C4700FP500 | 0603 | Vishay Beyschlag | MCT06030C4700FP500
150060RS75000 | Red 625nm LED Indication - Discrete 2V 0603 (1608 Metric) | 1 | SYSTEM_FAULT | Fitted | 150060RS75000 | 0603-RED-LED
826646-2 | Connector Header Through Hole 2 position 0.100" (2.54mm) | 1 | CN1 | Fitted | 826646-2 | HDR 1X2
0532610471 | PicoBlade 4 Position Right Angle Connector Header Surface Mount 0.049" (1.25mm) | 1 | P3 | Fitted | 0532610471 | PICOBLADE 4PIN RIGHT ANGLE | Molex | 0532610471 | Surface Mount
ADS1248IPW | 24 bit ADC Differential Input, SPI, 28-pin TSSOP | 1 | U5 | Fitted | ADS1248IPWR | TSSOP28 | Texas Instruments | ADS1248IPW
B220-13-F | DIODE SCHOTTKY 20V 2A B220-13-F | 1 | D10 | Fitted | B220-13-F | DO-214AA | Diodes | B220-13-F | Surface Mount
CMS06(TE12L,Q,M) | DIODE SCHOTTKY 30V 2A CMS06(TE12L,Q,M) | 1 | D3 | Fitted | CMS06(TE12L,Q,M) | cms06 | Toshiba | CMS06(TE12L,Q,M) | Surface Mount
DNP | DIODE SCHOTTKY 23V 1A SOD323F | 1 | D8 | Fitted | NSVR0320MW2T1G | SOD323F | ON Semiconductor | NSVR0320MW2T1G
DNP | Header, 3-Pin, Right Angle | 1 | UART | Fitted | 4-103327-5 | HDR 1X3 | TE Connectivity AMP | 4-103327-5 | Through Hole
DS2777G+ | Battery Management 2-Cell, Stand-Alone, Li+ Fuel-Gauge IC with Protector and Optional SHA-1 Authentication | 1 | U7 | Fitted | DS2777G+ | TDFN-14-EP_3x5 | Maxim | DS2775G+ | Surface Mount
FDS6898AZ | MOSFET 2N-CH 20V 9.4A 8SOIC | 1 | U6 | Fitted | FDS6898AZ | SOIC8 | ON Semiconductor / Fairchild | FDS6898AZ | Surface Mount
MSP430F6659IPZR | Imported | 1 | U12 | Fitted | MSP430F6659IPZR | PZ0100A_N | Texas Instruments | MSP430F6659IPZ | Surface Mount
PC104 | PC104 | 1 | PC104 | Fitted | SSW-126-01-G-D | PC104 | Samtec | SSW-126-01-G-D | Through Hole
RED | SMD Red LED | 1 | SYSTEM_ON | Fitted | LTST-C191KFKT | 0603-LED | Vishay Lite-On | LTST-C191KFKT | Surface Mount
REF5025AQDRQ1 | REF5025A-Q1 | 1 | U13 | Fitted | REF5025AQDRQ1 | SOIC-8 | Texas Instruments | REF5025AQDRQ1
TCA4311ADR | IC SIGNAL BUFFER I2C 8SOIC | 1 | U28 | Fitted | TCA4311ADR | SOIC8 | Texas Instruments | TCA4311ADR | Surface Mount
TPS5410QDRQ1 | TPS5410QDRQ1 | 1 | U3 | Fitted | TPS5410QDRQ1 | SO8 Power PAD | Texas Instruments | TPS5410QDRQ1 | Surface Mount
TPS5430QDDARQ1 | TPS5430QDDARQ1 | 1 | U10 | Fitted | TPS5430QDDARQ1 | SO8 Power PAD | Texas Instruments | TPS5430QDDARQ1 | Surface Mount

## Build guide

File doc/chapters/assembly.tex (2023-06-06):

%
% assembly.tex
%
% Copyright (C) 2021 by SpaceLab.
%
% EPS 2.0 Documentation
%
% This work is licensed under the Creative Commons Attribution-ShareAlike 4.0
% International License. To view a copy of this license,
% visit http://creativecommons.org/licenses/by-sa/4.0/.
%

%
% \brief Assembly instructions chapter.
%
% \author Gabriel Mariano Marcelino <gabriel.mm8@gmail.com>
% \author Yan Castro de Azeredo <yan.ufsceel@gmail.com>
%
% \institution Universidade Federal de Santa Catarina (UFSC)
%
% \version 0.2.0
%
% \date 2021/03/07
%

\chapter{Board Assembly} \label{ch:assembly}

\section{PCB Fabrication}

The board is not designed to be fabricated without a solder mask, but a Class 3 fabrication is recommended if possible. A list with the fabrication specifications can be seen in \autoref{tab:pcb-fabrication}, and layer stack-up can be seen in \autoref{tab:pcb-stackup}.

\begin{table}[!h]
    \centering
    \begin{tabular}{L{0.5\columnwidth}L{0.5\columnwidth}}
        \toprule[1.5pt]
        \textbf{Parameter}      & \textbf{Value} \\
        \midrule
        Size                    & 86.26 $\times$ 92.13 mm \\
        Layers                  & 4 \\
        Thickness               & 1.6 mm \\
        Minimum Hole Size       & 0.254 mm \\
        Maximum Hole Size       & 3.2 mm \\
        Silkscreen Color        & White \\
        Surface Finish          & HASL with lead \\
        Via Process             & Tenting vias \\
        Material                & FR-4: TG150 \\
        Minimum Track/Spacing   & 6/6 mil (0.1524/0.1524 mm)\\
        Solder Mask Color       & Green \\
        Gold Fingers            & No \\
        Impedance Control       & No \\   
        Fiducials               & 3 on top and bottom layers already placed \\
        Finish Copper           & Outer and inner copper 1 oz (35 $\mu$m Cu) \\
        \bottomrule[1.5pt]
    \end{tabular}
    \caption{PCB fabrication specifics.}
    \label{tab:pcb-fabrication}
\end{table}

\newpage

\begin{table}[!h]
    \centering
    \begin{tabular}{L{0.3\columnwidth}L{0.3\columnwidth}L{0.3\columnwidth}}
        \toprule[1.5pt]
        \textbf{Layer}  & \textbf{Material}   & \textbf{Thickness mm} \\
        \midrule
        Top Layer       & Cooper              & 0.035                   \\
        Dielectric 1    & Prepreg             & 0.12                    \\
        Signal Layer 1  & Cooper              & 0.035                   \\
        Core            & FR-4: TG-150         & 1.2                     \\
        Signal Layer 2  & Cooper              & 0.035                   \\
        Dielectric 2    & Prepreg             & 0.12                    \\
        Bottom Layer    & Cooper              & 0.035                   \\
        \bottomrule[1.5pt]
    \end{tabular}
    \caption{PCB stack up.}
    \label{tab:pcb-stackup}
\end{table}

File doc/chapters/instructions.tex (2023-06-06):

%
% instructions.tex
%
% Copyright (C) 2021 by SpaceLab.
%
% EPS 2.0 Documentation
%
% This work is licensed under the Creative Commons Attribution-ShareAlike 4.0
% International License. To view a copy of this license,
% visit http://creativecommons.org/licenses/by-sa/4.0/.
%

%
% \brief Instructions chapter.
%
% \author Gabriel Mariano Marcelino <gabriel.mm8@gmail.com>
%
% \institution Universidade Federal de Santa Catarina (UFSC)
%
% \version 0.2.0
%
% \date 2020/11/05
%

\chapter{Usage Instructions} \label{ch:instructions}

\section{Powering the Board}

The EPS 2.0 is the energy provider module within a satellite; its nominal operation is alongside a battery pack from the BAT4C module and solar panels. 

During development and testing, the board can also be partially powered using the JTAG interface (only the MCU and peripherals connected to the 3V3 EPS regulator) or fully powered directly through the battery connector with an equivalent power supply.

The module's PC104 power pins can be accessed externally, but it is advised to be used only for test probes and not powering directly from them. 

In the following subsections powering from the JTAG interface and batteries connector are explained in detail. 
It is advised to have the kill switches on the "NO" position and/or the RBF switch active before connecting the probes or cables to power the module.

% add real image of the IIP been used with EPS2
 
\subsection{Powering through JTAG Interface}

The JTAG interface is used for programming and debugging the module using a Flash Emulation Tool (refer to \autoref{jtag-picoblade} on the hardware chapter). 
This is done using a MSP-FET with the Spy-Bi-Wire protocol.
The tool should provide $3.3 V$ and a maximum of $100\ mA$; due to this current limitation, only the EPS MCU can be powered for minimal testing and debugging purposes; for this, the CN1 header pins must be shorted.
Remember that the CN1 connector should only be used if the EPS board is not powered by other means like batteries or external power supply.

For interfacing the 14 pin cable of the MSP-FET to the EPS, an adapted cable or an external interface is required. 
The IIP\cite{iip} Nº1 and Nº2 boards have a 14 pin header that translates in a picoblade connector for the required connector counterpart on the EPS module; any of the pin header slots from 1 to 4 can be used.
When the MSP-FET is correctly connected and the necessary cable connections are made, the kill switches can be put on the "NC" position, and/or the RBF switch can be released.
The 3V3 MCU (refer to \autoref{status-leds} on the system overview chapter) indicates that the 3.3V power is being sourced; the system on led can be checked to see any easily detectable misbehavior right after the programming of the board. 
%On \autoref{eps-iip-connection} shows the connection between EPS and IIP.

% add real image of the IIP been used with EPS2

\subsection{Powering through Power Supply}

Two voltage sources are needed to power the EPS module through an external power supply.
The external power sources can be set up in two ways, either two \(3.7 V\) sources in series or a \(3.7 V\) source for reference and a \(7.4 V\) source for power.
In both cases, the voltage sources should be connected to one of the battery board connectors (P1 or P5).

To use two \(3.7 V\) sources, the first source should have it's negative and positive terminals connected to Vbat- and Vbat\_common pins of the batteries connector respectively, the second source should have it's negative and positive terminals connected to Vbat\_common and Vbat+ pins of the batteries connector respectively (refer to \autoref{fig:battery-connector} and \autoref{tab:battery-connector} on the hardware chapter).

To use \(3.7 V\) and \(7.4 V\) sources, the \(3.7 V\) source should have its negative and positive terminals connected to Vbat- and Vbat\_common pins of the batteries connector, respectively, the \(7.4 V\) source should have it is negative and positive terminals connected to Vbat- and Vbat+ pins of the batteries connector respectively (refer to \autoref{fig:battery-connector} and \autoref{tab:battery-connector} on the hardware chapter).

Suppose the external power supply has configurable current limitation capability. In that case, it should be adjusted accordingly to the expected consumption of the load connected to the EPS module (other modules being powered by the EPS, batteries heaters being active, etc.); if powering the EPS in isolation (no load connected) a limit of \(80 mA\) may be applied.

After correctly connecting the voltage sources, the kill switches can be put on the "NC" position, and/or the RBF switch can be released.

% add appendix instructions for equivalent power supply powering

\subsection{Powering through Batteries}

To power the EPS module from the batteries, the BAT4C module must be connected through the P5 connector (refer to \autoref{fig:battery-connector} on the hardware chapter).
The batteries can be charged if needed using the P3 PicoBlade connector (refer to \autoref{external-charge-picoblade} on the hardware chapter), it will also require an external interface or an adapted cable to be used for interfacing the charger device to the PicoBlade.
The batteries also can be charged directly from the BAT4C module, for this refer to its documentation on the usage instruction chapter for more details \cite{bat4c}.

\section{Log Messages}

The EPS 2.0 has a UART interface for debugging, described in \autoref{tab:usci-config}. It follows a log system structure to improve the information provided in each message.
The messages can be acquired by connecting a USB cable to the IIP Nº3 board with an integrated FTDI FT4232H IC \cite{iip}.

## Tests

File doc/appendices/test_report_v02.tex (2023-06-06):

%
% test_report_v05.tex
%
% Copyright (C) 2021 by SpaceLab.
%
% EPS 2.0 Documentation
%
% This work is licensed under the Creative Commons Attribution-ShareAlike 4.0
% International License. To view a copy of this license,
% visit http://creativecommons.org/licenses/by-sa/4.0/.
%

%
% \brief Test report of the v0.1 hardware.
%
% \author André M. P. Mattos <andre.mattos@spacelab.ufsc.com>
%
% \institution Universidade Federal de Santa Catarina (UFSC)
%
% \version 0.1.0
%
% \date 2021/06/23
%

\chapter{Test Report of v0.2 Version} \label{anx:test-report-v02}

This appendix is a test report of the first manufactured and assembled PCB (version v0.2).

\begin{itemize}
    \item \textbf{PCB manufacturer}: PCBWay (China)
    \item \textbf{PCB assembly}: PCBWay (China)
    \item \textbf{PCB arrival date}: 2022/04/14 
    \item \textbf{Execution date}: 2022/04/15 to 2022/05/15
    \item \textbf{Tester}: João Cláudio and Ramon Borba
\end{itemize}

\section{Visual Inspection}

\begin{figure}[!ht]
    \begin{center}
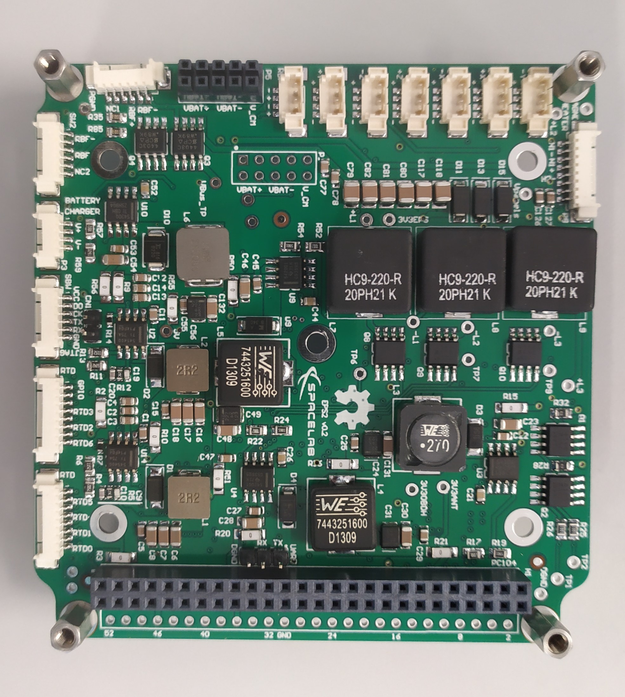
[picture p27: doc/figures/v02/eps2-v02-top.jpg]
        
        \caption{Top view of the EPS 2.0 v0.2 board.}
        \label{fig:eps2-v01-top}
    \end{center}
\end{figure}

\begin{figure}[!ht]
    \begin{center}
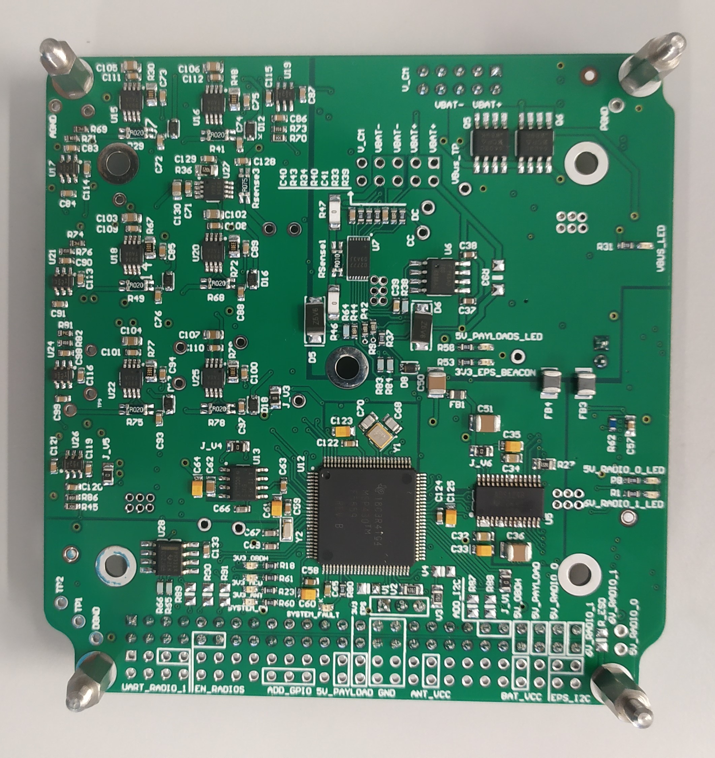
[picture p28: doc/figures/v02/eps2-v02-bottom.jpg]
        
        \caption{Bottom view of the EPS 2.0 v0.2 board.}
        \label{fig:eps2-v01-bottom}
    \end{center}
\end{figure}

\begin{itemize}
    \item \textbf{Test description/Objective}: Inspection of the board, visually, searching for fabrication and assembly failures.
    \item \textbf{Procedures:} \autoref{tab:visual-inspection}.
    \item \textbf{Material}: None.
    \item \textbf{Results}: First, the top and bottom side of the EPS 2.0 are shown in \autoref{fig:eps2-v01-top} (top view of the board) and \autoref{fig:eps2-v01-bottom} (bottom view of the board). It was possible to see that some components were not soldered. At the bottom side the R89, R90, R91, versioning resistors V1 and V4, R93, R87, R88, R\_ESD were not soldered. At the top side only half of the PC-104 and P1 were not connected. Furthermore, the P5 was connected in the wrong side.
    \item \textbf{Conclusion}: No major problems were identified on this test.  
\end{itemize}

\newpage

\section{Mechanical Inspection}

\begin{itemize}
    \item \textbf{Test description/Objective}: Evaluate if the board has the right dimensions and the necessary mechanical specs prior to integration.
    \item \textbf{Procedures:} \autoref{tab:mechanical-inspection}.
    \item \textbf{Material}: Pachymeter, rule and a digital scale.
    \item \textbf{Results}: The inspection was performed with the available tools. The board presented the right dimensions and has 90g.
    \item \textbf{Conclusion}: The board should not present any problem due to the heritage from the previous models and the good manufacturing quality.
\end{itemize}

\section{Integration Inspection}

\begin{itemize}
    \item \textbf{Test description/Objective}: Analyze the integration accordance prior to the module’s full assembly on the CubeSat.
    \item \textbf{Procedures:} \autoref{tab:integration-inspection}.
    \item \textbf{Material}: None.
    \item \textbf{Results}: Schematic files and pinout identified in the \autoref{ch:hardware}. 
    \item \textbf{Conclusion}: No problems were identified on this test, except from those found during the visual inspection.
\end{itemize}

\section{Electrical Inspection}

\begin{itemize}
    \item \textbf{Test description/Objective}: Inspect for visually detectable electrical errors.
    \item \textbf{Procedures:} \autoref{tab:electrical-inspection}.
    \item \textbf{Material}: None.
    \item \textbf{Results}: The top and bottom side of the EPS 2.0 are shown in \autoref{fig:eps2-v01-top} (top view of the board) and \autoref{fig:eps2-v01-bottom} (bottom view of the board).
    \item \textbf{Conclusion}: No problems were identified on this test, components were correctly selected, placed and soldered (except for those already mentioned in the visual inspection).
\end{itemize}

\newpage

\section{Electrical Testing}

\begin{figure}[!htb]
    \begin{center}
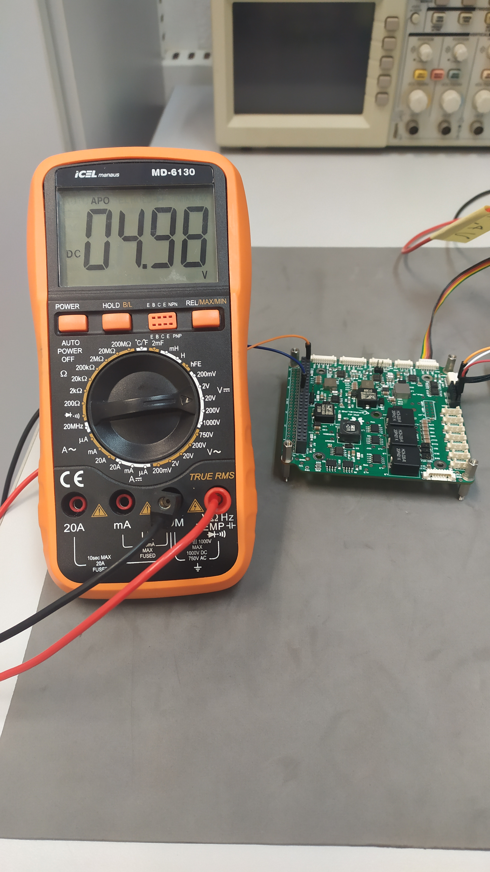
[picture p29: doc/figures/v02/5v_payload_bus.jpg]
        \subfigure[5V bus to the payload.\label{fig:5v_payload_bus}]{}
        \hspace{10pt}%
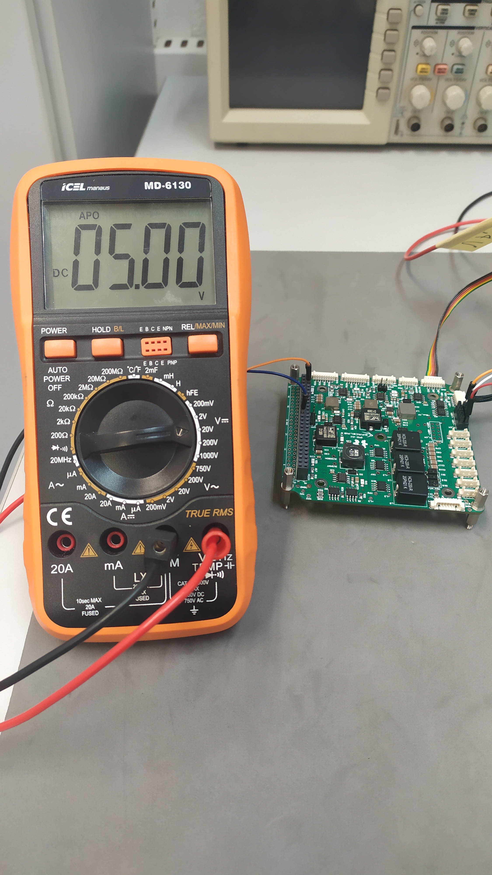
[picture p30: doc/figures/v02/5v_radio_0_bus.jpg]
        \subfigure[5V bus to the TTC.\label{fig:5v_radio_0_bus}]{} \\
        
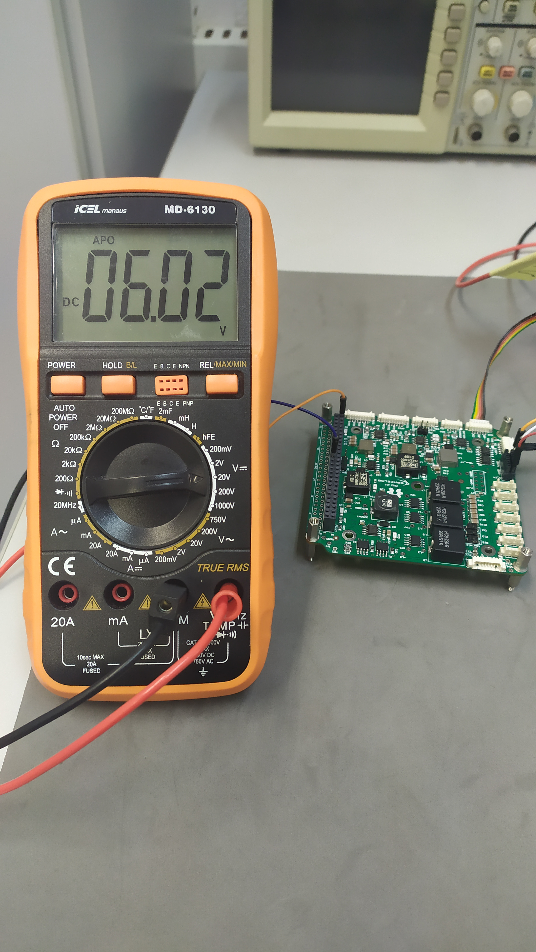
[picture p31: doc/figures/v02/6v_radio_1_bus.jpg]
        \subfigure[6V bus to the TTC.\label{fig:6v_radio_1_bus}]{}
        \hspace{10pt}%
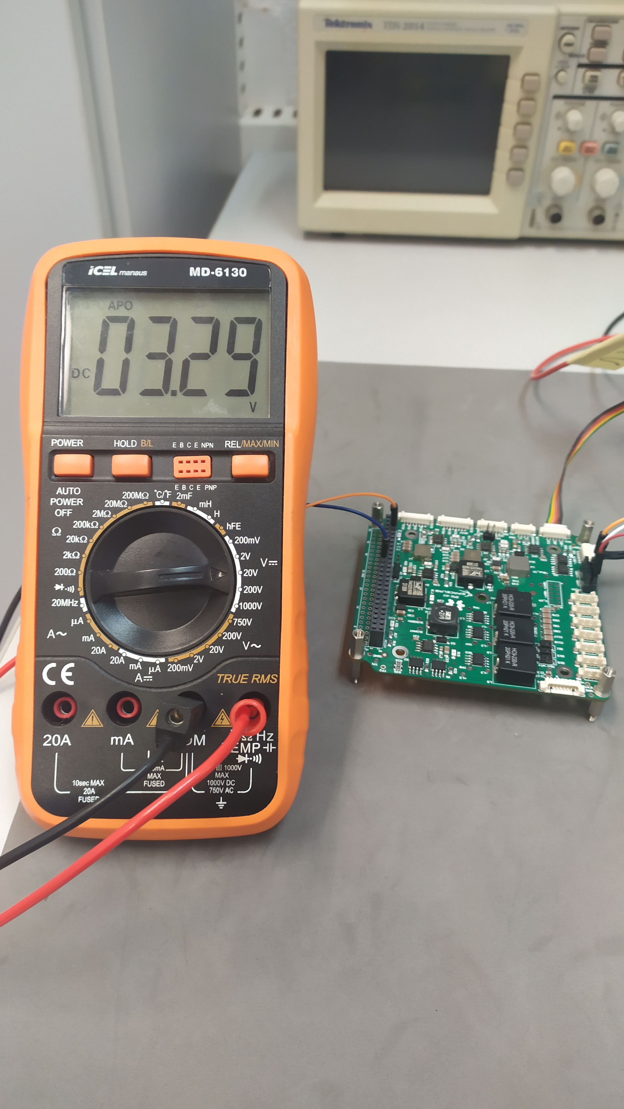
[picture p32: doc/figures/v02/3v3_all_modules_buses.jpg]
        \subfigure[3,3V bus to multiple modules.\label{fig:3v3_all_modules_buses}]{}        

        \caption{Measuring the voltage of the power buses without a load.}
        \label{fig:regulators_no_load}
    \end{center}
\end{figure}

\begin{itemize}
    \item \textbf{Test description/Objective}: Perform basic tests to evaluate the board with nominal operating parameters.
    \item \textbf{Procedures:} \autoref{tab:electrical-testing}.
    \item \textbf{Material}:
        \begin{itemize}
            \item Fluke's DMMs (Digital Multimeters) from 170 series
            \item N6705B, Keysigh's DC Power Analyser
        \end{itemize}
    \item \textbf{Results}: First, the multimeter was used to search for short circuits between the VCC and GND buses. Then, the EPS 2.0 was turned on with a power supply. Moreover, it was measured the voltage on the power buses without any load, which the results are presented in \autoref{fig:regulators_no_load}. Furthermore, a load was connected to these buses to evaluate if it would occur a voltage drop. The setup for 5V and 6V is shown in \autoref{fig:5v_6v_setup_test} and for 3,3V is shown on \autoref{fig:3v3_setup_test}. For these setups, the load would drain approximately 1A.
    \item \textbf{Conclusion}: The board turned on as expected and present stable power consumption. The voltage at the output of the step-down regulator of the 3,3V bus to power up the Beacon had a significant drop. The issue might be related to poor sizing of passive components required for the regulators. This problem \textbf{must} be solved for the next version (it is expected to be performed minor changes in components values).  
\end{itemize}

\begin{figure}[!ht]
    \begin{center}
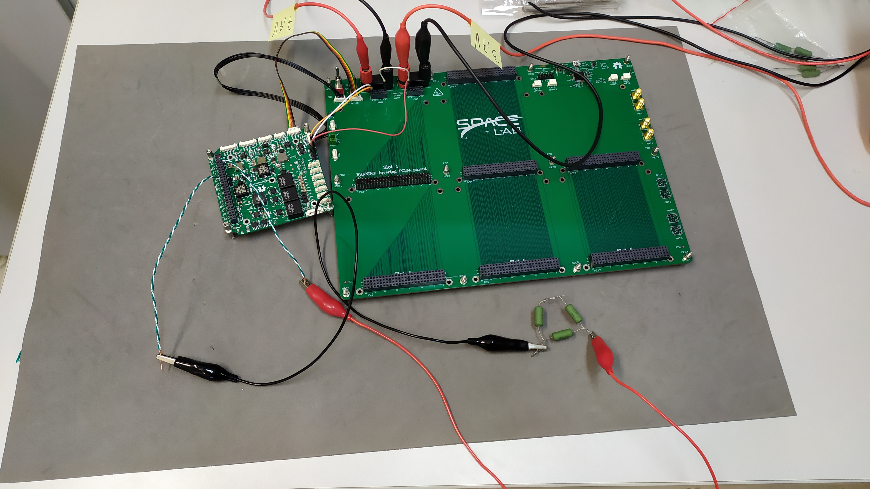
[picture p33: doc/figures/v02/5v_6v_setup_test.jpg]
        
        \caption{Setup to evaluate the 5V and 6V buses with load.}
        \label{fig:5v_6v_setup_test}
    \end{center}
\end{figure}

\newpage

\begin{figure}[!ht]
    \begin{center}
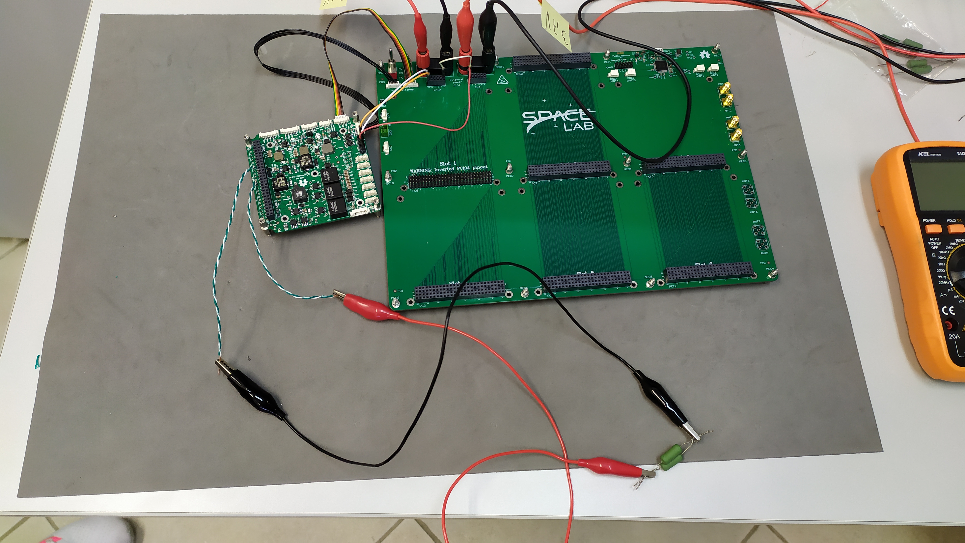
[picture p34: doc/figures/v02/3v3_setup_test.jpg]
        
        \caption{Setup to evaluate the 3,3V buses with load.}
        \label{fig:3v3_setup_test}
    \end{center}
\end{figure}

\section{Functional Testing}

\subsection{Firmware Programming}

\begin{figure}[!htb]
    \begin{center}
        \subfigure[Board connections using the MSP-FET and USB-UART converter.\label{fig:setup-first-boot}]{}
        ~
        \subfigure[Pin connections using the MSP-FET and USB-UART converter.\label{fig:electrical-test-board}]{}
        \caption{Setup used for the first firmware boot}
        \label{fig:setup-first-boot}
    \end{center}
\end{figure}

\begin{itemize}
    \item \textbf{Test description/Objective}: Evaluate the board behavior under a firmware programming sequence.
    \item \textbf{Material}:
        \begin{itemize}
            \item Code Composer Studio v10.0.0
            \item MSP-FET Flash Emulation Tool
            \item USB-UART converter
            \item PuTTy
        \end{itemize}
    \item \textbf{Results}: The results of this are available in \autoref{fig:log-first-boot}, where the log messages of the first boot of the board can be seen.
    \item \textbf{Conclusion}: Major problems were identified on this test, but it was expected since the available firmware version was at early stages of refactoring and development.
\end{itemize}

\begin{figure}[!ht]
    \begin{center}
        
        \caption{Log messages during the first boot.}
        \label{fig:log-first-boot}
    \end{center}
\end{figure}

\subsection{Communication Buses}

\begin{itemize}
    \item \textbf{Test description/Objective}: Test the communication buses of the board, as listed below:
        \begin{itemize}
            \item I$^{2}$C bus, to communicate with the OBDH
            \item UART bus, to communicate with the TTC
        \end{itemize}
    \item \textbf{Material}:
        \begin{itemize}
            \item Saleae Logic Analyzer (24 MHz, 8 channels)
            \item Saleae Logic software (v1.2.18)
            \item MSP-FET Flash Emulation Tool
        \end{itemize}
    \item \textbf{Results}: The results of this test can be seen in \autoref{fig:test-i2c} and \autoref{fig:test-uart}
    \item \textbf{Conclusion:} Minor problems were identified on this test, but were corrected. The figures shows the buses after the corrections, working as expected.
\end{itemize}

\begin{figure}[!htb]
    \begin{center}
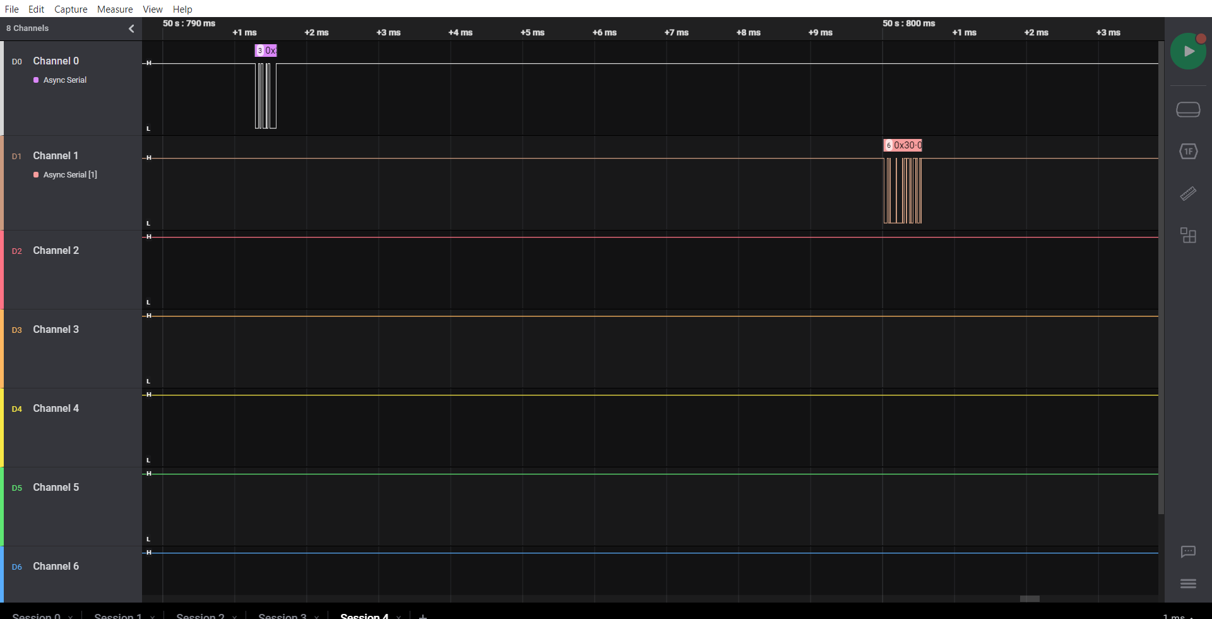
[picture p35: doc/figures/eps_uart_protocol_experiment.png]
        \subfigure[View of the communication.\label{fig:test-uart-1}]{}
        ~
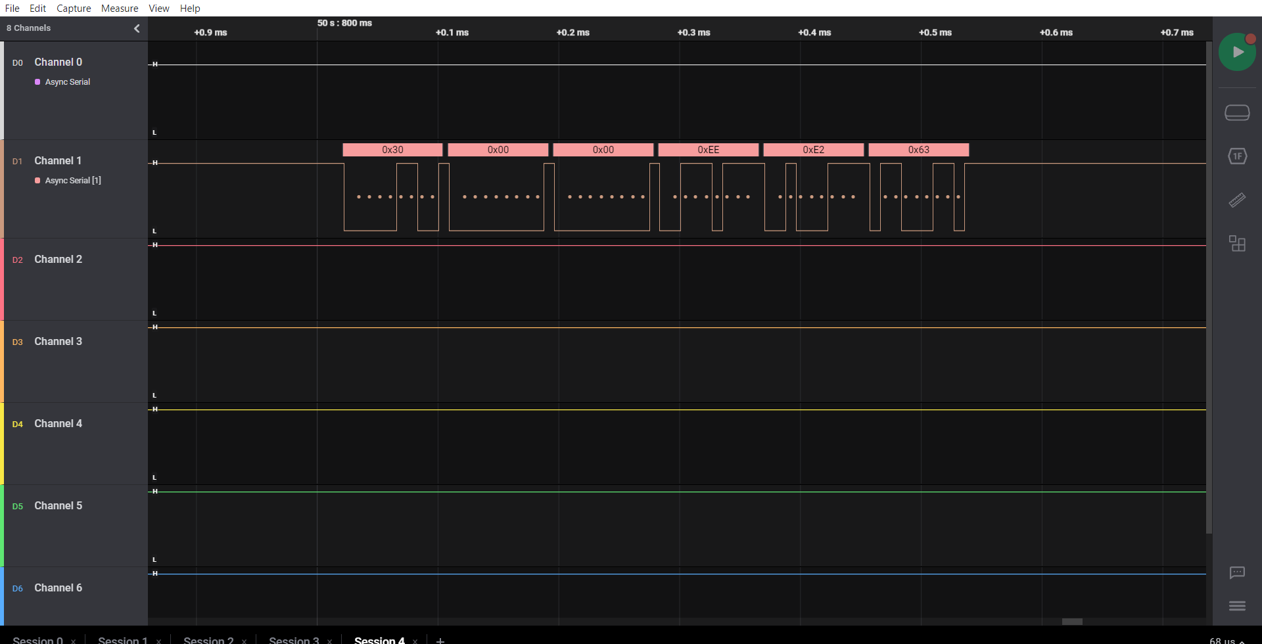
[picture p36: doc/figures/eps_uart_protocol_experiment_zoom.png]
        \subfigure[Zoom in the data sent by EPS.\label{fig:test-uart-2}]{}
        \caption{Communication between the TTC and EPS}
        \label{fig:test-uart}
    \end{center}
\end{figure}

\begin{figure}[!ht]
    \begin{center}
        
        \caption{Communication between the OBDH and EPS.}
        \label{fig:test-i2c}
    \end{center}
\end{figure}

\subsection{Sensors}

\begin{itemize}
    \item \textbf{Test description/Objective}: Test the EPSs' sensors, as listed below:
        \begin{itemize}
            \item Voltage sensors
            \item Current sensors
            \item Temperature sensors
        \end{itemize}
    \item \textbf{Material}:
        \begin{itemize}
            \item Code Composer Studio v9.3.0
            \item MSP-FET Flash Emulation Tool
            \item USB-UART converter
            \item Screen (Linux software)
        \end{itemize}
    \item \textbf{Results}: The values of current, voltage and temperature are correct. The temperature values are shown in \autoref{fig:test-temperature}. The values shown in the figure were obtained during the tests of the heater's on-off controller.
    \item \textbf{Conclusion:} In a first moment, the values of voltage and current were not correct, but it was figured out that the problem was in the firmware. The values of temperature were, in a first moment, all 0$^{\circ}$C. But, again, the problem was in the configuration of the ADS1248. When these problems were corrected, the values started to be correct.
\end{itemize}

\newpage

\begin{figure}[!ht]
    \begin{center}
        
        \caption{Values of temperature during the evaluation of heater's on-off controller.}
        \label{fig:test-temperature}
    \end{center}
\end{figure}

\subsection{Peripherals}

\subsection{Battery monitor}

\begin{itemize}
    \item \textbf{Test description/Objective}: Test the functionality of the DS2777.
    \item \textbf{Material}:
        \begin{itemize}
            \item Saleae Logic Analyzer (24 MHz, 8 channels)
            \item Saleae Logic software (v1.2.18)
            \item MSP-FET Flash Emulation Tool
        \end{itemize}
    \item \textbf{Results}: The results of this test can be seen in \autoref{fig:test-battery-monitor-1}, \autoref{fig:test-battery-monitor-2} and \autoref{fig:test-battery-monitor-3}.
    \item \textbf{Conclusion:} In a first moment, the CI was not working as expected. It was found that the Zener diode, D6, was interfering in the I$^{2}$C communication. It was removed and the CI started to work properly.  
\end{itemize}

\begin{figure}[!ht]
    \begin{center}
        
        \caption{First part of the log.}
        \label{fig:test-battery-monitor-1}
    \end{center}
\end{figure}

\begin{figure}[!ht]
    \begin{center}
        
        \caption{Second part of the log.}
        \label{fig:test-battery-monitor-2}
    \end{center}
\end{figure}

\newpage

\begin{figure}[!ht]
    \begin{center}
        
        \caption{Last part of the log.}
        \label{fig:test-battery-monitor-3}
    \end{center}
\end{figure}

\subsection{Heater's on-off controller}

\begin{itemize}
    \item \textbf{Test description/Objective}: Test the functionality of the heater's on-off controller.
    \item \textbf{Material}:
        \begin{itemize}
            \item Logs
            \item MSP-FET Flash Emulation Tool
        \end{itemize}
    \item \textbf{Results}: The results of this test can be seen in \autoref{fig:test-temperature-control}.
    \item \textbf{Conclusion:} The heater's on-off controller is working as expected. It was decided to used, during the tests in the workbench, thresholds such 26$^{\circ}$C and 32$^{\circ}$C.  
\end{itemize}

\begin{figure}[!ht]
    \begin{center}
        
        \caption{Temperature of the batteries being controlled.}
        \label{fig:test-temperature-control}
    \end{center}
\end{figure}

\subsection{MPPT controller}

\begin{itemize}
    \item \textbf{Test description/Objective}: Test the functionality of the MPPT controller.
    \item \textbf{Material}:
        \begin{itemize}
            \item Oscilloscope
            \item Unit tests
            \item MSP-FET Flash Emulation Tool
        \end{itemize}
    \item \textbf{Results}: The PWM signal generated by the MPPT controller can be seen in \autoref{fig:test-pwm-1} and \autoref{fig:test-pwm-2}, as well as the test workflow can be accessed in the GitHub page.
    \item \textbf{Conclusion:} The algorithm was tested using the unit tests, and worked as expected. The PWM signal for 100kHz and 50kHz are being generated correctly.  
\end{itemize}

\begin{figure}[!ht]
    \begin{center}
        
        \caption{PWM signal, at 50kHz, generated by the MPPT controller.}
        \label{fig:test-pwm-1}
    \end{center}
\end{figure}

\begin{figure}[!ht]
    \begin{center}
        
        \caption{PWM signal, at 100kHz, generated by the MPPT controller.}
        \label{fig:test-pwm-2}
    \end{center}
\end{figure}

\section{Conclusion} The board can be connected with the rest of the satellite, using a FlatSat platform, to make system level tests.

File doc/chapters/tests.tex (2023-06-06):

%
% tests.tex
%
% Copyright (C) 2021 by SpaceLab.
%
% EPS 2.0 Documentation
%
% This work is licensed under the Creative Commons Attribution-ShareAlike 4.0
% International License. To view a copy of this license,
% visit http://creativecommons.org/licenses/by-sa/4.0/.
%

%
% \brief Test procedures chapter.
%
% \author Yan Castro de Azeredo <yan.ufsceel@gmail.com>
%
% \institution Universidade Federal de Santa Catarina (UFSC)
%
% \version 0.2.0
%
% \date 2021/04/24
%

\chapter{Test Procedures} \label{ch:test-procedures}

This chapter follows a standard workflow created by SpaceLab for testing its CubeSat modules; these procedures are first referenced in FloripaSat-2 documentation chapter 7\cite{floripasat2-doc}. The \autoref{tab:test-procedures-table} resumes the workflow and each one of the test types, subtests, and code identification. Some subtests can be considered to be not applied to the platform; the order in which they are done does not need to follow the numeration, and others have generic titles that don't require too much explanation to be accomplished. The particularities of the EPS 2.0 for each test type are described in the following sections, and the results of those tests in the v0.1 and v0.2 versions of the EPS 2.0 are presented in the \autoref{anx:test-report-v01} and \autoref{anx:test-report-v02}.

\begin{table}[!h]
    \centering
    \begin{tabular}{l|p{105mm}|p{5mm}}
        \toprule[1.5pt]
        Test type     & Subtests & ID \\
        \midrule
        A. Visual Inspection     & 1. Packaging quality assessment \newline 2. Board manufacturing and assembly quality \newline 3. 3D model comparison \newline 4. Layers marker \newline 5. Labels (schematics comparison) \newline 6. High resolution photos for documentation & TA1 \newline TA2 \newline TA3 \newline TA4 \newline TA5 \newline TA6 \\
        \midrule
        B. Mechanical Inspection     & 1. Board dimensions and mounting holes positioning \newline 2. Board weight measurement & TB1 \newline TB2 \\
        \midrule
        C. Integration Inspection    & 1. Check connectors pinout against the documentation \newline 2. Check connectors positioning & TC1 \newline TC2 \\
        \midrule
        D. Electrical Inspection     & 1. Solder shorts \newline 2. Missing components \newline 3. Lifted pins \newline 4. Poor soldering \newline 5. Swapped components \newline 6. Components partnumber & TD1 \newline TD2 \newline TD3 \newline TD4 \newline TD5 \newline TD6 \\
        \midrule
        E. Electrical Testing       & 1. Continuity test \newline 2. Power up procedures \newline 3. Average input power consumption measurement \newline 4. Average output power source measurement \newline 5. Power tracks temperature \newline 6. Simple signal integrity & TE1 \newline TE2 \newline TE3 \newline TE4 \newline TE5 \newline TE6 \\
        \midrule
        F. Functional Testing     & 1. Simple test code run \newline 2. System code run \newline 3. System hardware self-test flags check \newline 4. Monitor LEDs behavior \newline 5. Monitor the debug serial port logs & TF1 \newline TF2 \newline TF3 \newline TF4 \newline TF5 \\
         \midrule
        G. Module Testing     & 1. Review operation behavior \newline 2. Review features and requirements fulfillment \newline 3. Review communication buses configuration and protocol \newline 4. Review data packages, power buses, and control signals \newline 5. Review edge cases and evaluate damage \newline 6. Run remote automated code tests \newline 7. Run system test codes in the board \newline 8. Run latest stable code version and review behavior & TG1 \newline TG2 \newline TG3 \newline TG4 \newline TG5 \newline TG6 \newline TG7 \newline TG8  \\
        \bottomrule[1.5pt]
    \end{tabular}
    \caption{Test workflow table.}
    \label{tab:test-procedures-table}
\end{table}

\section{Visual Inspection}

The first step when receiving a manufactured (and in some cases assembled) PCB is to inspect it visually to see if it is according to its expected appearance. The EPS 2.0 has more than 300 components, so it is advised for this test not to take a long time to accomplish; the major noted problems should be spotted and reported. The \autoref{tab:visual-inspection} resumes the visual inspection steps. 

\begin{table}[!htb]
\centering
\caption{Visual Inspection test steps.}
\label{tab:visual-inspection}
\begin{tabular}{m{3cm} m{12cm} m{3cm}}
\toprule
Test type & Visual Inspection \\
\midrule
\midrule
subtests code & Description \\ 
\midrule
TA1 & Verify the received package, review the packaging protection used, and if it maintained the physical and/or aesthetic integrity of the board. \\
\midrule
TA2 & See if the overall quality specified on the manufacturing process is according with its IPC class, the engineering model should be Class 2 while the flight model Class 3. \\
\midrule
TA3 & Inspect the top and bottom side of the PCB and verify if all the components are well soldered and if their polarity and labels are correct according to schematics and 3D model. Figure \ref{fig:pcb-top} and \ref{fig:pcb-bottom} for reference. If the board is not yet assembled detail, the inconsistencies found during the assembly process. \\
\midrule
TA4 & Take a high-resolution centered photo of both sides of the board for documentation; avoid reflections if possible. \\
\midrule
\midrule
Success Criteria & The board needs to appear functional regarding its visual electrical specs. \\
\bottomrule
\end{tabular}
\end{table}

\section {Mechanical Inspection}

These tests verify if the board has the expected mechanical specs before integration. The \autoref{tab:mechanical-inspection} resumes the mechanical inspection steps. 

\begin{table}[!htb]
\centering
\caption{Mechanical Inspection test steps.}
\label{tab:mechanical-inspection}
\begin{tabular}{m{3cm} m{12cm} m{3cm}}
\toprule
Test type & Mechanical Inspection \\
\midrule
\midrule
subtests code & Description \\ 
\midrule
TB1 & Verify board dimensions outline and mounting holes size and positioning with a measurement tool or through the board's draftsman sheet 1:1 scale print. \\
\midrule
TB2 & Measure board weight with an electronic balance with at least 0.1 grams of precision. \\
\midrule
\midrule
Success Criteria & The fabricated board needs to follow the mechanical specification of the draftsman document. \\
\bottomrule
\end{tabular}
\end{table}

\section{Integration Inspection}

These tests verify the integration before the module's full assembly on the CubeSat. The \autoref{tab:integration-inspection} resumes the integration inspection steps. 

\begin{table}[!htb]
\centering
\caption{Integration Inspection test steps.}
\label{tab:integration-inspection}
\begin{tabular}{m{3cm} m{12cm} m{3cm}}
\toprule
Test type & Integration Inspection \\
\midrule
\midrule
subtests code & Description \\ 
\midrule
TC1 & Check external connectors pinout labels against the documentation present on \autoref{external-connectors}. \\
\midrule
TC2 & Check connectors positioning and possible integration issues from connected cables with the mounted BAT4C board and solar panels. \\
\midrule
\midrule
Success Criteria & The labels and placement of the external connectors must be according to the documentation and not present any possible integration issues. \\
\bottomrule
\end{tabular}
\end{table}

\section {Electrical Inspection}

These tests verify if the components used in the mounted module are correct, if they are well-soldered and if there is any other error in the layout. \autoref{tab:electrical-inspection} resumes the electrical inspection steps.

\begin{table}[!htb]
\centering
\caption{Electrical Inspection test steps.}
\label{tab:electrical-inspection}
\begin{tabular}{m{3cm} m{12cm} m{3cm}}
\toprule
Test type & Electrical Inspection \\
\midrule
\midrule
Subtests code & Description \\ 
\midrule
TD1 & Check for any visible short circuit in the module buses. It is not necessary to use any equipment; it is a ``visual inspection" only. \\
\midrule
TD2 & Check if all the components were soldered. If there are missing components, it is necessary to evaluate if it was intended or not. \\
\midrule
TD3 & Check if the pins of the ICs and other components are damaged. \\
\midrule
TD4 & Check if there is any poor soldering. \\
\midrule
TD5 & Check if the components are swapped or connected ``backward". \\
\midrule
TD6 & Check the part number of the components. \\
\midrule
\midrule
Success Criteria & All the intended components are connected correctly to the board, without any visible errors. \\
\bottomrule
\end{tabular}
\end{table}

\section {Electrical Testing}

Now it is necessary to use equipment such multimeter, oscilloscope, power supply, or anything that can be used to evaluate the interface between components and connectors. \autoref{tab:electrical-testing} resumes the electrical testing steps.

\begin{table}[!htb]
\centering
\caption{Electrical Testing steps.}
\label{tab:electrical-testing}
\begin{tabular}{m{3cm} m{12cm} m{3cm}}
\toprule
Test type & Electrical Testing \\
\midrule
\midrule
Subtests code & Description \\ 
\midrule
TE1 & Using a multimeter, check for any short circuit in the buses of the module, primarily the power buses. \\
\midrule
TE2 & If the module does not present short circuits between GND and VCC signals, power up the module with a power supply to see if it turns on. \\
\midrule
TE3 & Check the power consumption of the module. \\
\midrule
TE4 & Check if the converters of the module are working as intended. \\
\midrule
TE5 & Check if the module is not overheating. \\
\midrule
TE6 & Check if the signals are being transmitted correctly through the buses. \\
\midrule
\midrule
Success Criteria & The modules do not present any short circuits and can be turned on without any critical problems. \\
\bottomrule
\end{tabular}
\end{table}

\section {Functional Testing}

It is necessary to evaluate if the module can run any code and if it is ready to be used during FSW development and debugging. \autoref{tab:functional-testing} resumes the functional testing steps.

\begin{table}[!htb]
\centering
\caption{Functional Testing steps.}
\label{tab:functional-testing}
\begin{tabular}{m{3cm} m{12cm} m{3cm}}
\toprule
Test type & Functional Testing \\
\midrule
\midrule
Subtests code & Description \\ 
\midrule
TF1 & Check if the module can run a code. Preferably something straightforward, such as a ``blinking LED". \\
\midrule
TF2 & Check if the module can run its firmware, even if it is incomplete. \\
\midrule
TF3 & Check if the module can make some self-tests. The results of these self-tests are going to be presented in its log. \\
\midrule
TF4 & Check if the LEDs are working as intended. \\
\midrule
TF5 & Check the logs for a longer period. \\
\midrule
\midrule
Success Criteria & The module has minimal expected functionalities. \\
\bottomrule
\end{tabular}
\end{table}
 
\section {Module Testing}

The module will be tested to evaluate if it can communicate with other modules, if its sensors are measuring all the variables correctly (e.g., voltage, current, temperature), and if it is operating as expected. \autoref{tab:module-testing} resumes the module testing steps.

\begin{table}[!htb]
\centering
\caption{Module Testing steps.}
\label{tab:module-testing}
\begin{tabular}{m{3cm} m{12cm} m{3cm}}
\toprule
Test type & Functional Testing \\
\midrule
\midrule
Subtests code & Description \\ 
\midrule
TG1 & Run and review the module's firmware and evaluate it using any equipment that SpaceLab offers. \\
\midrule
TG2 & Check and review the drivers, devices, and tasks to see if the features are correctly implemented. \\
\midrule
TG3 & Check and review the configuration of the communication protocols used. \\
\midrule
TG4 & Check and review all the buses to see if there is any anomaly or unexpected behavior. \\
\midrule
TG5 & Check and review the module's operation when submitting an edge situation. \\
\midrule
TG6 & Run the unit tests. \\
\midrule
TG7 & Run system test codes in the board. \\
\midrule
TG8 & Run the latest stable code version and review behavior. \\
\midrule
\midrule
Success Criteria & The is operating correctly. \\
\bottomrule
\end{tabular}
\end{table}

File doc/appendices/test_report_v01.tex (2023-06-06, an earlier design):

%
% test_report_v05.tex
%
% Copyright (C) 2021 by SpaceLab.
%
% EPS 2.0 Documentation
%
% This work is licensed under the Creative Commons Attribution-ShareAlike 4.0
% International License. To view a copy of this license,
% visit http://creativecommons.org/licenses/by-sa/4.0/.
%

%
% \brief Test report of the v0.1 hardware.
%
% \author André M. P. Mattos <andre.mattos@spacelab.ufsc.com>
%
% \institution Universidade Federal de Santa Catarina (UFSC)
%
% \version 0.1.0
%
% \date 2021/06/23
%

\chapter{Test Report of v0.1 Version} \label{anx:test-report-v01}

This appendix is a test report of the first manufactured and assembled PCB (version v0.1).

\begin{itemize}
    \item \textbf{PCB manufacturer}: PCBWay (China)
    \item \textbf{PCB assembly}: PCBWay (China)
    \item \textbf{PCB arrival date}: 2021/04/14
    \item \textbf{Execution date}: 2021/06/13 to 2021/07/01
    \item \textbf{Tester}: André M. P. Mattos
\end{itemize}

\section{Visual Inspection}

\begin{figure}[!ht]
    \begin{center}
        
        \caption{Top view of the EPS 2.0 v0.1 board.}
        \label{fig:eps2-v01-top}
    \end{center}
\end{figure}

\begin{figure}[!ht]
    \begin{center}
        
        \caption{Bottom view of the EPS 2.0 v0.1 board.}
        \label{fig:eps2-v01-bottom}
    \end{center}
\end{figure}

\begin{itemize}
    \item \textbf{Test description/Objective}: Inspection of the board, visually and with a multimeter, searching for fabrication and assembly failures.
    \item \textbf{Procedures:} \autoref{tab:visual-inspection}.
    \item \textbf{Material}: None.
    \item \textbf{Results}: The results of this test can be seen in Figures \ref{fig:eps2-v01-top} (top view of the board) and \ref{fig:eps2-v01-bottom} (bottom view of the board).
    \item \textbf{Conclusion}: No major problems were identified on this test, just some labels with typos (all in the PC-104 region) that should be already be corrected for v0.2 and four 4-pin picoblades that were not soldered by the manufacturer due the lack of clearance (differently from the headers and PC-104 which were intentionally removed from the process). This last item might be ignored since the manufacturer used an automated soldering process and the manual placement of these connectors is totally feasible.  
\end{itemize}

\section{Mechanical Inspection}

\begin{itemize}
    \item \textbf{Test description/Objective}: Evaluate if the board has the nominal mechanical specs prior to integration.
    \item \textbf{Procedures:} \autoref{tab:mechanical-inspection}.
    \item \textbf{Material}: None.
    \item \textbf{Results}: The inspection was not performed due to the lack of the proper tools.
    \item \textbf{Conclusion}: Even without the test, the board should not present any problem due to the heritage from the previous models and the good manufacturing quality.
\end{itemize}

\section{Integration Inspection}

\begin{itemize}
    \item \textbf{Test description/Objective}: Analyze the integration accordance prior to the module’s full assembly on the CubeSat.
    \item \textbf{Procedures:} \autoref{tab:integration-inspection}.
    \item \textbf{Material}: None.
    \item \textbf{Results}: Schematic files and pinouts identified in the \autoref{ch:hardware}. 
    \item \textbf{Conclusion}: No problems were identified on this test.
\end{itemize}

\section{Electrical Inspection}

\begin{itemize}
    \item \textbf{Test description/Objective}: Inspect the visually detectable electrical features.
    \item \textbf{Procedures:} \autoref{tab:electrical-inspection}.
    \item \textbf{Material}: None.
    \item \textbf{Results}: The results of this test can be seen in Figures \ref{fig:eps2-v01-top} (top view of the board) and \ref{fig:eps2-v01-bottom} (bottom view of the board).
    \item \textbf{Conclusion}: No problems were identified on this test, components were correctly selected, placed and soldered (except for those already mentioned in the visual inspection).
\end{itemize}

\section{Electrical Testing}

\begin{itemize}
    \item \textbf{Test description/Objective}: Perform basic tests to evaluate the board with nominal operating parameters.
    \item \textbf{Procedures:} \autoref{tab:electrical-testing}.
    \item \textbf{Material}:
        \begin{itemize}
            \item Multimeter Fluke 179
            \item Keysight N6705B DC Power Analyzer
        \end{itemize}
    \item \textbf{Results}: Results reported with the following images: \ref{fig:electrical-test-setup}, \ref{fig:power-consumption}, \ref{fig:regulator-payload}, \ref{fig:regulator-antenna}, \ref{fig:regulator-radio0}, \ref{fig:regulator-radio1}, \ref{fig:regulator-obdh} and \ref{fig:regulator-epsttc}. 
    \item \textbf{Conclusion}: The boards power-up as expected and present stable power consumption. The power outputs (step-down regulators) underperform with nominal or slightly higher load parameters. The issue might be related to poor sizing of passive components required for the regulators. This problem \textbf{must} be solved for the next version (it is expected to be performed minor changes in components values).  
\end{itemize}

\begin{figure}[!htb]
    \begin{center}
        \subfigure[Test setup for power characterization.\label{fig:electrical-test-tools}]{}
        ~
        \subfigure[Board connectors and harness used during the tests.\label{fig:electrical-test-board}]{}
        \caption{Electrical test setup of the power-up sequence and output power supply channels.}
        \label{fig:electrical-test-setup}
    \end{center}
\end{figure}

\begin{figure}[!ht]
    \begin{center}
        
        \caption{Power consumption during standby with any intensive firmware task.}
        \label{fig:power-consumption}
    \end{center}
\end{figure}

\begin{figure}[!htb]
    \begin{center}
        \subfigure[Load: 0mA.\label{fig:regulator-payload-0mA}]{}
        ~
        \subfigure[Load: 500mA.\label{fig:regulator-payload-500mA}]{}
        ~
        \subfigure[Load: 1000mA.\label{fig:regulator-payload-1000mA}]{}
        ~
        \subfigure[Load: 1500mA.\label{fig:regulator-payload-1500mA}]{}
        
        \caption{Payload step-down regulator power characterization.}
        \label{fig:regulator-payload}
    \end{center}
\end{figure}

\begin{figure}[!htb]
    \begin{center}
        \subfigure[Load: 0mA.\label{fig:regulator-antenna-0mA}]{}
        ~
        \subfigure[Load: 500mA.\label{fig:regulator-antenna-500mA}]{}
        ~
        \subfigure[Load: 1000mA.\label{fig:regulator-antenna-1000mA}]{}
        ~
        \subfigure[Load: 1500mA.\label{fig:regulator-antenna-1500mA}]{}
        
        \caption{Antenna step-down regulator power characterization.}
        \label{fig:regulator-antenna}
    \end{center}
\end{figure}

\begin{figure}[!htb]
    \begin{center}
        \subfigure[Load: 0mA.\label{fig:regulator-radio0-0mA}]{}
        ~
        \subfigure[Load: 500mA.\label{fig:regulator-radio0-500mA}]{}
        ~
        \subfigure[Load: 1000mA.\label{fig:regulator-radio0-1000mA}]{}
        ~
        \subfigure[Load: 1500mA.\label{fig:regulator-radio0-1500mA}]{}
        
        \caption{Radio 0 step-down regulator power characterization.}
        \label{fig:regulator-radio0}
    \end{center}
\end{figure}

\begin{figure}[!htb]
    \begin{center}
        \subfigure[Load: 0mA.\label{fig:regulator-radio1-0mA}]{}
        ~
        \subfigure[Load: 500mA.\label{fig:regulator-radio1-500mA}]{}
        ~
        \subfigure[Load: 1000mA.\label{fig:regulator-radio1-1000mA}]{}
        ~
        \subfigure[Load: 1500mA.\label{fig:regulator-radio1-1500mA}]{}
        
        \caption{Radio 1 step-down regulator power characterization.}
        \label{fig:regulator-radio1}
    \end{center}
\end{figure}

\begin{figure}[!htb]
    \begin{center}
        \subfigure[Load: 0mA.\label{fig:regulator-obdh-0mA}]{}
        ~
        \subfigure[Load: 500mA.\label{fig:regulator-obdh-100mA}]{}
        ~
        \subfigure[Load: 1000mA.\label{fig:regulator-obdh-200mA}]{}
        ~
        \subfigure[Load: 1500mA.\label{fig:regulator-obdh-500mA}]{}
        
        \caption{OBDH step-down regulator power characterization.}
        \label{fig:regulator-obdh}
    \end{center}
\end{figure}

\begin{figure}[!htb]
    \begin{center}
        \subfigure[Load: 0mA.\label{fig:regulator-epsttc-0mA}]{}
        ~
        \subfigure[Load: 500mA.\label{fig:regulator-epsttc-500mA}]{}
        ~
        \subfigure[Load: 1000mA.\label{fig:regulator-epsttc-1000mA}]{}

        \caption{EPS/TTC step-down regulator power characterization.}
        \label{fig:regulator-epsttc}
    \end{center}
\end{figure}
 
 \newpage

\section{Functional Testing}

\subsection{Firmware Programming}

\begin{itemize}
    \item \textbf{Test description/Objective}: Evaluate the board behavior under a firmware programming sequence.
    \item \textbf{Material}:
        \begin{itemize}
            \item Code Composer Studio v10.0.0
            \item MSP-FET Flash Emulation Tool
            \item USB-UART converter
            \item PuTTy
        \end{itemize}
    \item \textbf{Results}: The results of this are available in \autoref{fig:log-first-boot}, where the log messages of the first boot of the board can be seen.
    \item \textbf{Conclusion}: Major problems were identified on this test, but it was expected since the available firmware version was at early stages of refactoring and development.
\end{itemize}

\begin{figure}[!htb]
    \begin{center}
        \subfigure[Board connections using the MSP-FET and USB-UART converter.\label{fig:setup-first-boot}]{}
        ~
        \subfigure[Pin connections using the MSP-FET and USB-UART converter.\label{fig:electrical-test-board}]{}
        \caption{Setup used for the first firmware boot}
        \label{fig:setup-first-boot}
    \end{center}
\end{figure}

\begin{figure}[!ht]
    \begin{center}
        
        \caption{Log messages during the first boot.}
        \label{fig:log-first-boot}
    \end{center}
\end{figure}
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

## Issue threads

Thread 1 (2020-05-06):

Hardware: Review the components parameters

andrempmattos, 2020-05-06:
Review the components parameters (check the partnumbers, comments, values and etc).

Tip: Enumerate here the components designators with inconsistency.

YanAzer, 2020-05-09:
**RTD1, RTD2 and P8**: Wrong 3D models, 3D models are not right angle but vertical (partnumber: 0532610871).
**R_ESD**: Wrong comment, ESD protection resistor is not 1M ohms, but 100K ohms or 0.1M ohms (partnumber: AC0805FR-13100KL).
**R87 to R91**: Wrong description and design item ID, SMD Jumper resistors have 1/8W rated power dissipation and not 1/16W specified in comments section (partnumber: CRCW08050000Z0EA).

Finished EPS_INTERFACE schematic sheet.

YanAzer, 2020-05-10:
**J_V5**: Wrong description and design item ID, SMD Jumper resistors have 1/8W rated power dissipation and not 1/16W specified in comments section (partnumber: CRCW08050000Z0EA).
**L7, L8 and L9**: Wrong description, the inductors are from HC9 series and not DR127 series.
**C79 to C81, C117, C118**: Wrong design item ID, the correct should be something like: Cap_Cer_X7R_22uF_25V_1210.

Finished 1_Measurement_and_MPPT shematic sheet.

YanAzer, 2020-05-10:
**R85**: Missing “1/10W” to comment, R35 has it.
**R46,R47 and R93**: Wrong description and design item ID, power dissipation should be 3/4W and not 1/2W (https://www.digikey.com/product-detail/en/vishay-dale/CRCW12060000Z0EAHP/541-0-0UBCT-ND/2222920)
R33, R42 and R44: Wrong description and design item ID, power dissipation should be 1/10W and not 1/8W (https://www.digikey.com/product-detail/en/vishay-dale/CRCW0603150RFKEAC/541-4023-1-ND/7928706)

 Finished 2_Battery_Monitoring_And_ Switches schematic sheet.

YanAzer, 2020-05-10:
Inside 3_MCU_EPS schematic sheet:

**J_V3 and J_V4**: Wrong description and design item ID, SMD Jumper resistors have 1/8W rated power dissipation and not 1/16W (https://www.digikey.com/product-detail/en/vishay-dale/CRCW08050000Z0EA/541-0-0ACT-ND/1180267).
**R65 and R66**: Wrong description and design item ID, SMD Jumper resistors have 0.15W rated power dissipation and not 1/8W = 0.125W (https://www.digikey.com/product-detail/en/vishay-beyschlag/MCT0603MC1002FP500/MCT0603-10-0K-MFCT-ND/3883103).
**R62**: Wrong description and design item ID, SMD Jumper resistors have 0.15W rated power dissipation and not 1/8W = 0.125W (https://www.digikey.com/product-detail/en/vishay-beyschlag/MCT0603MD4702DP500/MCT0603-47K-MDCT-ND/2092130).
**P11**: **SUGESTION** No relevant description text, suggestion: “SWITCH TACTILE SPST-NO 0.05A 12V”, maybe this doesn’t even matter anyway (https://www.digikey.com/product-detail/en/omron-electronics-inc-emc-div/B3U-1000P/SW1020CT-ND/1534357).

YanAzer, 2020-05-10:
Inside 4_Battery_Heater_Controller schematic sheet:

**J_V1, J_V6, R28 and R32**: Wrong description and design item ID, SMD Jumper resistors have 1/8W rated power dissipation and not 1/16W (https://www.digikey.com/product-detail/en/vishay-dale/CRCW08050000Z0EA/541-0-0ACT-ND/1180267).
**C126 and C127**: Wrong value of capacitance in comment, description and design item ID, **these components are also obsolete** (https://www.digikey.com/product-detail/en/murata-electronics/GRM216R71H103KA01D/490-1664-1-ND/587472).
**C36**: Wrong value of rated voltage in comment, description and design item ID. The right value is 10V (https://www.digikey.com/product-detail/en/murata-electronics/GRM31CR71A226KE15L/490-5309-1-ND/2039088).

Closed 2020-05-10.

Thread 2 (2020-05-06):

Hardware: Review the components obsolescence

andrempmattos, 2020-05-06:
Review if the components are available in Mouser or Digikey.

YanAzer, 2020-05-10:
No obsolete components found on EPS_INTERFACE schematic sheet.

YanAzer, 2020-05-10:
Inside 1_Measurement_and_MPPT shematic sheet:

**C72 to 78, C83 to C91, C93, C94, C97 to C101, C108 to C116**: Component obsolete https://www.digikey.com/product-detail/en/murata-electronics/GRM188R71H104KA93D/490-1519-1-ND/587854. **Too many components and they are not ordered! Might missed one…**
**C102 to C107**: Component obsolete https://www.digikey.com/product-detail/en/murata-electronics/GRM21BR71E475KA73L/490-9962-1-ND/5026449
**DQ8, DQ9 and DQ10**: https://www.digikey.com/product-detail/en/vishay-siliconix/SI4010DY-T1-GE3/SI4010DY-T1-GE3TR-ND/6834463

YanAzer, 2020-05-10:
Inside 2_Battery_Monitoring_And_ Switches schematic sheet:

**C40, C41 and C119 to C121**:  https://www.digikey.com/product-detail/en/murata-electronics/GRM188R71H104KA93D/490-1519-1-ND/587854
**C37 and C38**: https://www.digikey.com/product-detail/en/murata-electronics/GRM188R71H102KA01D/490-1494-1-ND/587851

YanAzer, 2020-05-10:
Inside 3_MCU_EPS schematic sheet:

**C58, C59, C62, C63, C122, C124 and C133**: https://www.digikey.com/product-detail/en/murata-electronics/GRM188R71H104KA93D/490-1519-1-ND/587854

YanAzer, 2020-05-10:
Inside 4_Battery_Heater_Controller schematic sheet:

**C32, C34, C126 and C127**: https://www.digikey.com/product-detail/en/murata-electronics/GRM216R71H103KA01D/490-1664-1-ND/587472.

Closed 2020-05-10.

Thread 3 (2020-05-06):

Hardware: Review the exported bill of materials

andrempmattos, 2020-05-06:

YanAzer, 2020-05-16:
**+X, +Y, +Z, P3, RBF, -X, -Y, -Z**: Designators without problems.
**+X_CSR, +Y_CSR, +Z_CSR, -X_CSR, -Y_CSR, -Z_CSR**: Designators without problems.
**3V3_ANT, 3V3_EPS, 3V3_MCU, 3V3_OBDH, 5_V, 5V_BEACON_LED, 5V_MAIN_RADIO_LED, VBus**: Designators without problems.
**C62,C77,C78**: have the old obsolete partnumber (https://www.digikey.com/product-detail/en/murata-electronics/GRM188R71H104KA93D/490-1519-1-ND/587854) instead of the supposed new one (https://www.digikey.com/product-detail/en/yageo/CC0805KRX7R9BB104/311-1140-1-ND/303050)
**C3, C4, C13, C14, C102, C103, C104, C105, C106, C107, C130**: Designators without problems.
**C6, C7, C8, C16, C17, C18, C30, C48, C131, C132**: Designators without problems.
**C9, C19**: Designators without problems.
**C10, C20**: Designators without problems.
**C21, C26, C32, C34, C44, C52**: Designators without problems.
**C23, C28, C46, C54**: Designators without problems.
**C24, C31, C49, C56**: Does these components have the right footprint? Curretly they are using 1210 package size (https://www.digikey.com/product-detail/en/panasonic-electronic-components/6TPE220MAZB/P16245CT-ND/4146688)
**C33, C35, C60, C61, C64, C123, C125**: Wrong comment, it is 6.3V and not 10V, these issue is better referenced in #1 (https://www.digikey.com/product-detail/en/avx-corporation/TPSR106K006R1000/478-9265-1-ND/4562130)
**C36, C50, C51, C79, C80, C81, C82, C117, C118**: Designators without problems.
**C37, C38**: Designators without problems.
**C39, C65**: Designators without problems.

YanAzer, 2020-05-20:
**C40, C41, C58, C59, C63, C71, C72, C73, C74, C75, C76, C83, C84, C85, C86, C87, C88, C89, C90, C91, C93, C94, C97, C98, C99, C100, C101, C108, C109, C110, C111, C112, C113, C114, C115, C116, C119, C120, C121, C122, C124, C128, C129, C133**: Designators without problems.
**C57**: Designator without problem.
**C66**: Designator without problem.
**C67, C69**: Designators without problems.
**C68, C70**: Designators without problems.
**D1, D2**: Designators without problem.
**D3**: Designator without problem.
**D4, D9, D11, D13, D15**: Designators without problems.
**D5, D6**: Designators without problems.
**D8**: Wrong voltage in description and design item ID, it is 20V and not 23V (https://www.digikey.com/product-detail/en/on-semiconductor/NSVR0320MW2T1G/NSVR0320MW2T1GOSCT-ND/5213359)
**D10**: Designator without problem.
D17, D18, D19, D20, D21, D22: wrong voltage in description and design item ID, it is 20V and not 23V (https://www.digikey.com/product-detail/en/on-semiconductor/NSVR0320MW2T1G/NSVR0320MW2T1GOSCT-ND/5213359)

YanAzer, 2020-05-21:
**FB1**: Wrong current in description and design item ID, should be 4A #1 (https://www.digikey.com/product-detail/en/murata-electronics/BLM21PG300SN1D/490-1052-1-ND/584499).
**FB3, FB4**: Designators without problem.
**J_V1, J_V3, J_V5, J_V6, R28, R32, R87, R88, R89, R90, R91**: Designators without problem.
**J_V4**: Designator without problem.
**L1, L2**: Wrong “DC Resistance (DCR)” in comment and design item ID, should be “15.5mOhm Max” #1 (https://www.digikey.com/product-detail/en/bourns-inc/SRP6540-2R2M/SRP6540-2R2MCT-ND/3986035).
**L3**: Designator without problem.
**L4, L5**: Wrong ““DC Resistance (DCR)” in design item ID, should be “34.5mOhm” #1 (https://www.digikey.com/product-detail/en/w%C3%BCrth-elektronik/7443251600/732-4180-1-ND/3476496).
**L6**: Wrong inductance value in comment, should be 10uH and not 2.2uH #1  (https://www.digikey.com/product-detail/en/vishay-dale/IHLP3232DZER100M11/541-1346-1-ND/2616984).
**L7, L8, L9**: Designators without problem.
**P5**: Designators without problem.
**P8, RTD1, RTD2**: Wrong 3D model already noticed in #1, for this particular case it will stay this way.
** P11**: Designator without problem.
**PC104**: Designator without problem.
**Q1 and Q2**: Obsolete partnumber #2 (https://www.digikey.com/product-detail/en/vishay-siliconix/SI4010DY-T1-GE3/SI4010DY-T1-GE3TR-ND/6834463) new one should be (https://www.digikey.com/product-detail/en/vishay-siliconix/SI4166DY-T1-GE3/SI4166DY-T1-GE3CT-ND/3305374) this one is on Q8, Q9 and Q10.
**Q3, Q4, Q5, Q6**: Nothing wrong.

YanAzer, 2020-05-26:
**R65 and R66**: Have the partnumber (https://www.digikey.com/product-detail/en/vishay-beyschlag/MCT0603MC1002FP500/MCT0603-10-0K-MFCT-ND/3883103) while the rest of the similar resistors [**R1, R8, R18, R23, R31, R53, R58, R61**] have the partnumber (https://www.digikey.com/product-detail/en/vishay-beyschlag/MCT06030C1001FP500/MCT0603-1-00K-CFCT-ND/2607875).
**R2, R3, R9, R10, R15, R16, R20, R21, R46, R47, R50, R51, R55, R56, R93**: Designators without problem.
**R4, R11**: Designators without problem.
**R5, R12**: Designators without problem.
**R6, R13**: partnumber not available in Digi-key (https://br.mouser.com/ProductDetail/Yageo/AC0805FR-0711K5L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)
**R7, R14**: Designators without problem.
**R17, R22, R52, R57**: Designators without problem.
**R19, R24, R54**: Designators without problem.
**R25, R26**: Designators without problem.
**R27**: Designator without problem.
**R33, R42, R44**: Designators without problem.
**R34, R37, R39, R40, R43, R60**: Designators without problem.
**R35, R85**: Designators without problem.
**R36**: Designator without problem.
**R45, R70**: Designators without problem.
**59**:  Designator without problem.
**62**: Wrong power in description and design item ID, it should be 0,15W and not 1/8W = 0,125W
**R63, R64**: Designators without problem.
**R67, R68, R72, R75, R79, R83**: Designators without problem.
**R69, R74, R81**: Designators without problem.
**R71, R73, R76, R82, R86**: Designators without problem.
**R_ESD**: Designator without problem.

YanAzer, 2020-05-27:
**Rsense3**: Designator without problem.
**RSense1**: Designator without problem.
** SBW, SW1, SW2**:
** SYSTEM_ON**: Wrong color of the led, should be orange (https://www.digikey.com/product-detail/en/lite-on-inc/LTST-C191KFKT/160-1445-1-ND/386832).
**U2, U14**: In Digi-key: “Not Recommended for New Design, minimums may apply. See Alternate Package or Substitute options” (https://www.digikey.com/product-detail/en/texas-instruments/TPS54540QDDARQ1/296-38301-1-ND/4967506).
**U3**: Not necessary the use of the SO8 Powed PAD footprint, the 8-SOIC package would be more compatible with the component (https://www.digikey.com/product-detail/en/texas-instruments/TPS5410QDRQ1/296-25229-1-ND/2174999).
**U4, U9**: Not necessary the use of the SO8 Powed PAD footprint, the 8-SOIC package would be more compatible with the components (https://www.digikey.com/product-detail/en/texas-instruments/TPS5420QDRQ1/296-23226-1-ND/1830821).
**U5**: Designator without problem.
**U6**: Designator without problem.
**U7**: Designator without problem.
**U10**: Designator without problem.
**U12**: Designator without problem.
**U13**: Designator without problem.
**U15, U16, U18, U20, U22, U25, U27**: Designators without problem.
**U17, U19, U21, U24, U26**: Designators without problem.
**U28**: Designator without problem.
**Y1**: Designator without problem.
**Y2**: Designator without problem.

YanAzer, 2020-07-07:
Found components for substitution and fixing obsolescence:

**C62, C77, C78**: [GRM188R71H104KA93D](https://www.digikey.com/product-detail/en/murata-electronics/GRM188R71H104KA93D/490-1519-1-ND/587854) **old** -> [GRM188R72A104KA35D](https://www.digikey.com/product-detail/en/murata-electronics/GRM188R72A104KA35D/490-3285-2-ND/702549) **new**

**Q1, Q2**: [SI4010DY-T1-GE3](https://www.digikey.com/product-detail/en/vishay-siliconix/SI4010DY-T1-GE3/SI4010DY-T1-GE3TR-ND/6834463) **old** -> [SI4166DY-T1-GE3](https://www.digikey.com/product-detail/en/vishay-siliconix/SI4166DY-T1-GE3/SI4166DY-T1-GE3CT-ND/3305374) **new**

Closed 2020-09-01.

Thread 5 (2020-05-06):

Hardware: Review the schematic sheets and layout design

andrempmattos, 2020-05-06:

YanAzer, 2020-07-13:
Added missing parameters in schematic library (ca01563e51dedf48082ea72989e9a1b2b7d73ad6), updated schematics from new library (a8c75fbee1973019a17b049bacdbf650ca93c521) and fixed component obsolescence (3effca03818f240b0ceb648794b145c6065add9c).

Closed 2020-09-01.

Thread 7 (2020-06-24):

Hardware: Check if is necessary update the PC104 connector

andrempmattos, 2020-06-24:

YanAzer, 2020-07-13:
The current PC104 connector has the old partnumber (https://www.digikey.com/product-detail/en/samtec-inc/SSW-126-01-G-D/SAM1208-26-ND/1112032), same as previous EPS 1.0 module. By contrast the OBDH 2.0 uses the right PC104 partnumber (https://www.digikey.com/product-detail/en/samtec-inc/ESQ-126-39-G-D/SAM10462-ND/3601055). Changing only the partnumber should solve the bug.

The visual 3D models are simplayed below, the difference in height is noticeable. @andrempmattos

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

andrempmattos, 2020-08-29:
Component updated! Using SSW-126-01-G-D

Closed 2020-08-29.

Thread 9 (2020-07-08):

Hardware: Make "fitted" and "not fitted" variants

YanAzer, 2020-07-08:
This feature will help to automated the generating of BOM and schematics with a "X" marker in DNP components.

Source; https://www.altium.com/documentation/altium-designer/workspacemanager-dlg-variantmanagementformvariant-management-ad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,such%20as%20the%20component's%20value.

YanAzer, 2020-07-22:
Sheet results of Draftsman file considering the "Test Model" variant, in red is representing the DNP components:

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

Closed 2021-06-15.

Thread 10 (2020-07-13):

Hardware: Make positional re-annotation in pcb layout

YanAzer, 2020-07-13:
This can make it easier to find components on the PCB.
Source: https://www.altium.com/documentation/altium-designer/pcb-dlg-setupannotatepositional-re-annotate-ad

YanAzer, 2021-05-26:
For the current state of the project this issue is not valid anymore.

Closed 2021-05-26.

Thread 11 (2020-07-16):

Hardware: Place "simple" fiducials components (one sided)

YanAzer, 2020-07-16:
Fiducials must be components placed in schematic to avoid its removal when updating the pcb document.

andrempmattos, 2020-08-31:
46071871a44eb37b06dd1ff611e1f4f49de81f1c
2705b1cc4ef4c0536867092fd3f30787f07f2876

Closed 2020-08-31.

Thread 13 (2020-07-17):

Hardware: Place other battery connector interface in schematic

YanAzer, 2020-07-17:
This will make EPS 2 compatible with both battery board 1.0 and battery board 2.0, currently when updating the pcb one of them disappears because it is not on schematic.

Closed 2020-08-29.

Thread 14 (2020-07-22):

Hardware: generate pick and place file considering variants and DNP components

YanAzer, 2020-07-22:
In a automated PCB assembly the variants are necessary to avoid placement of DNP components.

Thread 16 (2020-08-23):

Hardware: Add the option to increase the output voltage of the beacon bus

mgm8, 2020-08-23:
To increase or decrease the output voltage of the buses, a few componentes must be changed in each converter. To reach the desired output power on the radio of the beacon, its input voltage must be increased to 5,5 or 6 V (TBD).

The output voltage value can be increased by changing the value of L1, R4 and R6. Check the datasheet of the converter to define the new values.

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

Converter datasheet: [https://www.ti.com/lit/ds/symlink/tps54540-q1.pdf](https://www.ti.com/lit/ds/symlink/tps54540-q1.pdf)

andrempmattos, 2020-08-31:
- Example circuit: (RLS=R6 and RHS=R5)

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

- The output in function of the RLS and RHS resistors:
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

- Following the datasheet instructions and maintaining previous decisions: (in our circuit)
RLSbefore=R6=**11.5k** -> RLSafter=**11.5k** (Output=**5V**)
RHSbefore=R4=**60.4k** -> RLSafter=**74.75k** (Output=**6V**)

Closed 2020-09-01.

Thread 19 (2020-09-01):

Hardware: Add final BOM file using the newer SpaceLab template

andrempmattos, 2020-09-01:
Obs: Remeber to update schematics pdf and full pdf .
Obs2: Use [no variation] for the output file.

YanAzer, 2020-09-06:
Generating the BOM it was discovered that two components were missing the Partnumber, image is displayed below:

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

The cause of this bug probably is that the excel template uses the parameter "Partnumber" and not "Manufacturer Part Number", almost all components have these both parameters except the 3k3 and 47k resistors. Easiest solution would be adding a new parameter "Partnumber" to these few components, for the future it could be better if the teamplate actually tries to find both parameters.

Note: When using the "Part Search" or "Manufacturer Part Search" tool the default parameter linked is "Manufacturer Part Number".

Closed 2020-09-12.

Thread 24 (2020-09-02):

Firmware: Develop a driver for the DS2775G+ IC

mgm8, 2020-09-02:
[https://br.mouser.com/datasheet/2/256/DS2775-DS2778-1513647.pdf](https://br.mouser.com/datasheet/2/256/DS2775-DS2778-1513647.pdf)

YanAzer, 2021-03-23:
@AugustoVassoler can we close this issue? It may have still compilation errors found when debugging on CSS.

AugustoVassoler, 2021-03-23:
Yes. The next errors will appear during the test routine run and/or hardware running, and can be referenced in new issues.

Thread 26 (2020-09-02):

Firmware: Develop a driver for the TLV341A IC

mgm8, 2020-09-02:
[https://www.ti.com/product/TLV341A](https://www.ti.com/product/TLV341A)

YanAzer, 2021-04-02:
There is no need for a driver for the TLV341A IC since the shutdown pin is conected to 3v3.

Closed 2021-04-02.

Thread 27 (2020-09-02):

Firmware: Develop a driver for the MAX9934 IC

mgm8, 2020-09-02:
[https://datasheets.maximintegrated.com/en/ds/MAX9934.pdf](https://datasheets.maximintegrated.com/en/ds/MAX9934.pdf)

YanAzer, 2021-03-23:
@vinepb can we close this issue?

vinepb, 2021-03-23:
yes

Closed 2021-08-11.

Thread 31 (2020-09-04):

Firmware: Develop a driver for the TPS54540-Q1 IC

mgm8, 2020-09-04:
[https://www.ti.com/lit/ds/slvsc56b/slvsc56b.pdf](https://www.ti.com/lit/ds/slvsc56b/slvsc56b.pdf)

YanAzer, 2021-03-23:
@vinepb can we close this issue?

vinepb, 2021-03-23:
yes

YanAzer, 2021-04-02:
@vinepb i think we can rename this driver because EPS has one TPS5410QDRQ1, two TPS5420QDRQ1, one TPS5430QDDARQ1 and two TPS54540QDDARQ1 dc-dc buck converters. My sugestion is to rename this driver for something like "tps54" to be used for all these converters ICs.

mgm8, 2021-04-02:
@YanAzer "tps54x0" is a common choice for this type of situation.

Closed 2021-06-28.

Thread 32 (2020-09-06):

Firmware: Develop the battery manager device

mgm8, 2020-09-06:

AugustoVassoler, 2021-02-10:
SHA-d2a2d53

AugustoVassoler, 2021-02-10:
d2a2d53026ce6c3ddc803d27ccef7ee01d682e50

YanAzer, 2021-04-09:
@AugustoVassoler i think we can remove [these structures](https://github.com/spacelab-ufsc/eps2/blob/a343ee4a43b830af6df45c001b02d7c2375bc579/firmware/devices/bat_manager/bat_manager.h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) of the device, since now we have them on the [application layer](https://github.com/spacelab-ufsc/eps2/blob/dev_firmware/firmware/app/structs/eps2_data.h#L74-L97).

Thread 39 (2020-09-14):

Hardware: Add pull-up/down resistors in the regulador enable pins

andrempmattos, 2020-09-14:

YanAzer, 2021-06-03:
@andrempmattos this issue is still valid?

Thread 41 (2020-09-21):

Hardware: Fix the PC-104 connector BOM quantity and designator label

andrempmattos, 2020-09-21:

YanAzer, 2021-03-13:
Fixed BOM quantity in 500dd8af0f3906d9da8ba963ca1412b6a4f47e22.

Closed 2021-06-16.

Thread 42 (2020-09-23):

Hardware: Fix the BOM generation to group components using partnumber instead of comments

andrempmattos, 2020-09-23:

YanAzer, 2021-06-16:
This issue was already fixed in some unreferenced commit @andrempmattos

Closed 2021-06-16.

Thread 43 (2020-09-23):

Documentation: Add an option sheet to the main documentation

mgm8, 2020-09-23:
Add an option sheet (as an appendix) with instructions about the necessary components for each optional circuit or montage.

YanAzer, 2021-07-01:
@mgm8 is this issue still relevant?

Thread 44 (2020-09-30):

Hardware: Increase the maximum current of the blocking diodes

mgm8, 2020-09-30:
The current model has a maximum continuous current of 1 A. This value must be increased to at least 2 A (with 2 solar panels in parallel, the maximum nominal current can reach 1 A or more).

> Blocking diodes designator: D17 to D22

YanAzer, 2021-03-08:
Is this issue still relevant? If i am not mistaken the solar panels already include these blocking diodes, can you guys confirm @mgm8  @andrempmattos? Found an option [SMD22WS-TP](https://www.digikey.com/en/products/detail/micro-commercial-co/SMD22WS-TP/8554705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) anyway.

mgm8, 2021-03-08:
Yes, most commercial solar panels already include blocking diodes. In the FM we will probably replace these diodes by 0R jumpers (or even remove it from the project). For now we can replace the part number, but we will have to think about removing it or not soon.

Closed 2021-06-15.

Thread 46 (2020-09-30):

Hardware: Fix the blocking diodes part number in the BOM

mgm8, 2020-09-30:
The current BOM available [here](https://github.com/spacelab-ufsc/eps2/blob/master/hardware/outputs/board_schematics/board_full_pdf.pdf) describes the D17-D22 diodes as LEDs. The correct part number is [NSVR0320MW2T1G](https://www.onsemi.com/pub/Collateral/NSR0320MW2T1-D.PDF)

This issue is related to #44 and #45.

Closed 2021-06-15.

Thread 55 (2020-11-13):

Firmware: Define the system tasks

mgm8, 2020-11-13:

mgm8, 2020-11-18:
@YanAzer Preliminary list of tasks (more details in 53f2689):

* Startup (boot)
* Watchdog reset
* Periodic system reset
* Battery heater control
* Read sensors
* CSP server

> **TODO**: List all available data and sensors in the EPS module

YanAzer, 2020-11-20:
@mgm8 @andrempmattos some other tasks that may be missing:

• MPPT
• Energy level
• Send data Beacon
• Send data OBDH

Also a first list of available data (related to sensors) and sensors in the EPS module:

Data:
• Batteries temperature
• Battteries voltage
• Batteries current
• Solar panels temperature
• Solar panel pair voltage
• Individual solar panels current
• MCU internal temperature
• Main bus voltage

Sensors:
• RTDs
• Current sensors
• Voltage sensors
• Battery monitoring IC

andrempmattos, 2021-08-02:
Current tasks list:
- Startup (boot)
- Watchdog reset
- Periodic system reset
- Battery management
- Battery heater control
- MPPT algorithm
- Read sensors
- Parameter server
- _[CSP server]_ (probably won't be implemented)

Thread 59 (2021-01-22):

Firmware: Implement I2C slave scheme for OBDH communications

andrempmattos, 2021-01-22:
Implement a scheme for handling communications in slave mode:

Tip:
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

**Interrupt handler** (ISR in the image):

```c
void interrupt_handler(uint8_t *rx_buff, uint32_t rx_size)
{
	BaseType_t xHigherPriorityTaskWoken;

	/* The xHigherPriorityTaskWoken parameter must be initialized to pdFALSE as
	it will get set to pdTRUE inside the interrupt safe API function if a
	context switch is required. */
	xHigherPriorityTaskWoken = pdFALSE;

	/* 'Give' the semaphore to unblock the task, passing in the address of
	xHigherPriorityTaskWoken as the interrupt safe API function's
	pxHigherPriorityTaskWoken parameter. */
	xSemaphoreGiveFromISR( xBinarySemaphore, &xHigherPriorityTaskWoken );

	/* Pass the xHigherPriorityTaskWoken value into portYIELD_FROM_ISR(). If
	xHigherPriorityTaskWoken was set to pdTRUE inside xSemaphoreGiveFromISR()
	then calling portYIELD_FROM_ISR() will request a context switch. If
	xHigherPriorityTaskWoken is still pdFALSE then calling
	portYIELD_FROM_ISR() will have no effect. */
	portYIELD_FROM_ISR( xHigherPriorityTaskWoken );
}
```

**The handler task** (task 2 in the image):

```c
void vTaskHandler(void *pvParameters)
{
    while(1)
    {
    	/* This binary semaphore is used to wait for the interrupt event release.
    	The task blocks indefinitely, meaning this function call will only return
    	once the semaphore has been successfully obtained.*/
		xSemaphoreTake(xBinarySemaphore, portMAX_DELAY);

		/* To get here the event must have occurred. */
         ...
```

YanAzer, 2021-04-06:
@vinepb i suggest we remove the [i²c driver](https://github.com/spacelab-ufsc/eps2/tree/dev_firmware/firmware/drivers/i2c) importated from OBDH and leave the i²c_slave, also the current driver needs some fixing.

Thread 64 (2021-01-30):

Firmware: Develop the voltage sensor device

YanAzer, 2021-01-30:
Look at [OBDH2 devices](https://github.com/spacelab-ufsc/obdh2/tree/dev_firmware/firmware/devices) for reference.

Closed 2021-08-12.

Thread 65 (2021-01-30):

Firmware: Develop the current sensor device

YanAzer, 2021-01-30:
Look at [OBDH2 devices](https://github.com/spacelab-ufsc/obdh2/tree/dev_firmware/firmware/devices) for reference.

Closed 2021-08-12.

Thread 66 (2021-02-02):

Hardware: Add draftsman document of the board

YanAzer, 2021-02-02:
Follow the same model as [OBDH2](https://github.com/spacelab-ufsc/obdh2/blob/master/hardware/outputs/board_draftsman/board_draftsman.PDF), this issue is also connected to https://github.com/spacelab-ufsc/eps2/issues/9.

andrempmattos, 2021-06-06:
@YanAzer, can we close this issue?

Closed 2021-06-06.

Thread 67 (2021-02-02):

Hardware: Add missing BOM to fabrication folder

YanAzer, 2021-02-02:

Closed 2021-06-06.

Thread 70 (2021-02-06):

Hardware: Evaluate power for additional payloads

YanAzer, 2021-02-06:
On the EPS 2.0 board there are four 5V power pins for payloads with only one regulator IC. It needs to be evaluated if is necessary to add another voltage regulator in case of up to four payloads to be powered from the system.

andrempmattos, 2021-06-06:
I guess in our current development stage, it is more feasible to keep this payload power scheme. Adding more regulators in this board will only "overcomplicate" its busy design.

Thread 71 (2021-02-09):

Firmware: Update SPI driver for EPS2

YanAzer, 2021-02-09:
The current SPI driver is from OBDH2, this makes it incoherent with the actual hardware usage on EPS2. The EPS2 uses a dedicated SPI to communicate with ADS1248 device, the CS is on the GPIO pin number 59.

Closed 2021-08-06.

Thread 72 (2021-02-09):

Hardware: Fix/Improve status leds silkscreen labels

YanAzer, 2021-02-09:
Missing silkscreen labels to beacon and main radio status leds:
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

Improve "5_V" led to "5V_PAYLOADS_LED"
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

Closed 2021-06-06.

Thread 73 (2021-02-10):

Firmware: Develop the heater device

mgm8, 2021-02-10:
Develop a device to handle the battery heater.

andrempmattos, 2021-08-04:
@joaoclaudioeb, check if we **must** use float variables! If so, which is the impact using the MSP430? Can we simplify the algorithm and use only intergers?

mgm8, 2021-08-04:
> @joaoclaudioeb, check if we **must** use float variables! If so, which is the impact using the MSP430? Can we simplify the algorithm and use only intergers?
>
> For example, can we work with variables in other units, such as: (temperature * 100) or (temperature in kelvin) ?

If it's necessary to work float variables, using fixed-point arithmetic will save some resources: [https://www.best-microcontroller-projects.com/fixed-point.html](https://www.best-microcontroller-projects.com/fixed-point.html)

Working with other units (Kelvin instead of Celsius as example) is also a good approach.

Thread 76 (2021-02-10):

Firmware: Develop a device for the TTC

mgm8, 2021-02-10:
This device is an abstraction of the TTC module and will be used for the communication with the TTC.

AugustoVassoler, 2021-02-17:
CSP reference: https://github.com/GomSpace/libcsp

AugustoVassoler, 2021-04-22:
f2365b2b0e8ddba76d0ed9ab5c1fa42e70d8f0ae

andrempmattos, 2021-08-02:
Observation: Now TTC requires UART "breakchar" in the end of each communication session (i.e., each "adr+data+crc" or "adr+crc" burst).

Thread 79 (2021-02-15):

Firmware: Configure the github actions to enable CI/HIL with a self-hosted runner

YanAzer, 2021-02-15:
The idea is to perform CI and HIL using the self-hosted runner connected to the OBDH board. This issue is equal to https://github.com/spacelab-ufsc/obdh2/issues/206

Closed 2021-08-12.

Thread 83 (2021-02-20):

Documentation: List all variables from the sensors and peripherals of the EPS

mgm8, 2021-02-20:
Add a table with all possible variables that can be read from the sensors and peripherals of the EPS.

YanAzer, 2021-03-02:
Preliminary list:

**From current sensors on solar panels input (measured by EPS2 MCU):**
- Current solar panel pair side -Y
- Current solar panel pair side +Y
- Current solar panel pair side -X
- Current solar panel pair side +X
- Current solar panel -Z
- Current solar panel +Z

**From voltage sensors on solar panels input (measured by EPS2 MCU):**
- Voltage solar panels -Y and +X
- Voltage solar panels -X and +Z
- Voltage solar panels -Z and +Y
- Voltage output from boosters

**From current sensor on EPS/Beacon regulator (measured by EPS2 MCU):**
- Current from EPS2 circuitry and Beacon MCU;

**From voltage sensors on main power buss (measured by EPS2 MCU):**
- Voltage from main power buss (VBUS)

**From batteries monitor IC (measured by itself):**
- Voltage from positive side of the batteries (+VBAT)
- Voltage from common reference of the batteries (VBAT common)
- Batteries curret and average current
- Battery monitor IC temperature

**From RTDs on the batteries board (measured by external ADC IC):**
- Heaters temperature (RTDs)

**From EPS2 MCU (measured by itself):**
- Internal EPS2 MCU temperature

Note: some variables from the battery monitoring IC were not considered such as:

- Batteries monitor status register
- Batteries monitor cycle counter
- Batteries monitor remaining active absolute capacity register
- Batteries monitor remaining standby absolute capacity register
- Batteries monitor remaining active relative capacity register
- Batteries monitor remaining standby relative capacity register

@mgm8 @AugustoVassoler @vinepb

mgm8, 2021-03-04:
@YanAzer Suggestion: Add an ID number for each variable (16-bits?), and the length, in bytes, of each variable.

andrempmattos, 2021-08-02:
@mgm8 and @YanAzer, is this issue finished?

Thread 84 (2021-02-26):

Hardware: Include partnumber in the comments of DNP components

YanAzer, 2021-02-26:
Some connectors that are DNP don't have their partnumber, making it difficult to identify for reference in BOMs without opening the schematic on altium to look at the parameters.

andrempmattos, 2021-06-06:
J_V4 should have a DNP indication

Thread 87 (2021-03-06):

Documentation: Add the fabrication details of the PCB

mgm8, 2021-03-06:
* Material
* Number of layers
* Board thickness
* Recomended surface finishing
* Minimum spacing
* Via process
* Copper weight
* etc.

Closed 2021-06-28.

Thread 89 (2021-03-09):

Firmware: Develop the read sensors task

YanAzer, 2021-03-09:
The read sensors task is periodic executing in every 60000 milliseconds.

andrempmattos, 2021-07-05:
@YanAzer, you might increase this frequency to provide updated values for both (OBDH and TTC) in any time...

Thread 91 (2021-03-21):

Readme: Update mission link name on main readme on the notes header

YanAzer, 2021-03-21:
Currently is still using the old link, it work but the name is wrong.

Closed 2021-06-28.

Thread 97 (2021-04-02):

Add missing I2C buffer circuit to mcu diagram

YanAzer, 2021-04-02:
Update diagram on the hardware schematic and documentation.

Closed 2021-06-28.

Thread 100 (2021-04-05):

Hardware: Review the comments and description of the schematic components

YanAzer, 2021-04-05:
Some components may still have misleading comments and description, an example is L6 inductor of the payload regulator circuit. This issue is associated with: https://github.com/spacelab-ufsc/eps2/issues/3

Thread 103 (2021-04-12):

Hardware: Evaluate component values used in the current sensor circuit

YanAzer, 2021-04-12:
This time the EPS will be receiving twice the current because of two solar panels in parallel, evaluate the values used and see what it needs to be changed.

YanAzer, 2021-05-05:
Prelimary evaluation resulted in the change of both Rsense and Rout to maintain the same measurement caracteristics from previous EPS project:
- Rsense = 20mΩ
- Rout = 4kΩ

For this values and with a fixed Vout = 3V (different from the previous project that was 2.5V) and considering a current load of 1.5A (worst case for this situation) with the formulas from the MAX9934 datasheet results:

- Iout = 750uA (same as EPS 1.0)
- Vsense = 30mV (same as EPS 1.0)
- Psense = 45mW (EPS 1.0 1.8mW considering a current load of only 600mA)

Values of Rout below 4kΩ would result in a greater current output of  750uA from the MAX9934, it is not certain the maximum limits for this parameter, but this value is the same constraint used in the EPS 1.0 project.

YanAzer, 2021-05-12:
@mgm8 @andrempmattos my calculations seem right? If not, well, it will be just boring desoldering these resistors afterwords...

andrempmattos, 2021-06-06:
@YanAzer, I think yout assumption that Vout might be 3V need a review. The VREF+ uses the external voltage reference circuit that generates 2V5 in the output. I think the absolute maximum rate of the ADC input is the AVCC supply (3V3), but to have readable value the max output in the ADC pins should be 2V5. Please, check that before the next release.

In page 48 you will find more info: https://www.ti.com/lit/ds/symlink/msp430f6659.pdf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

Voltage reference circuit: https://www.ti.com/product/REF5025A-Q1

YanAzer, 2021-06-06:
@andrempmattos thanks for the feedback, you are correct, redoing the previous calculations with the same parameters and Vout = 2.5V we obtain: Rsense = 20.2mΩ and Rout = 3.3kΩ. I will be improving this part for the documentation too.

Closed 2021-06-14.

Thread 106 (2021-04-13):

Documentation: Add the firmware abstraction layers diagram

YanAzer, 2021-04-13:

YanAzer, 2021-06-11:
Suggestions:
- Change task "read sensors" name to "housekepping" @mgm8
- Change "OBDH package" and "Beacon package" to one task called "communication handler" (or maybe something shorter) @andrempmattos

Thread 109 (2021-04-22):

Hardware: Fix "board_prints" output to include the middle layers (currently only top/bottom are printed)

andrempmattos, 2021-04-22:

Closed 2021-06-16.

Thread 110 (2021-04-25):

Documentation: Write the "tests" chapter

YanAzer, 2021-04-25:
This chapter will describe the particularities of the module in perspective of the topics of the test workflow first mentioned in the FloripaSat-2 documentation:

Visual Inspection:
  - Packaging quality assessment
  - Board manufacturing and assembly quality
  - 3D model comparison
  - Layers marker
  - Labels (schematics comparison)
  - High resolution photos for documentation

  Mechanical Inspection:
  - Board dimensions and mounting holes positioning
  - Board weight measurement

  Integration Inspection:
  - Check connectors pinout against the documentation (not schematics)
  - Check connectors positioning (if applicable)

  Electrical Inspection:
  - Solder shorts
  - Missing components
  - Lifted pins
  - Poor soldering
  - Swapped components
  - Components partnumber

  Electrical Testing:
  - Continuity test
  - Power up procedures (check LEDs and testpoints)
  - Average input power consumption measurement
  - Average output power source measurement (if applicable)
  - Power tracks temperature (if applicable)
  - Simple signal integrity (if applicable)

  Functional Testing:
  - Run a simple test code (if applicable)
  - Run the system code (if applicable and available)
  - Check the system hardware self-test flags (if applicable and available)
  - Monitor basic LEDs behavior (if applicable)
  - Monitor the debug serial port logs (if applicable)

  Module Testing:
  - Review operation behavior against the documentation (if applicable)
  - Review features and requirements fulfillment
  - Review communication buses configuration and protocol (if applicable)
  - Review data packages, power buses and control signals
  - Review edge cases and evaluate damage
  - Run remote automated code tests (if applicable)
  - Run system test codes in the board (if applicable)
  - Run latest stable code version, monitor logs and qualify behavior (if applicable)

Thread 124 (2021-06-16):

Hardware: Fix fabrication information on sheet layer for flight model

YanAzer, 2021-06-16:
Details such as: surface treatment, pcb color and specified no silkcreen need to be updated. Adding IPC class 3 specification may be useful.

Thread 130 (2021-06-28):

Documentation: Update hardware chapter with changes done in v0.2

YanAzer, 2021-06-28:
- [x] Update I²C interface for DS2777
- [x] #127
- [x] Update radio transceivers regulator names
- [x] Update image for battery monitor
- [x] Cite pin header jumper for MSP-FET and MCU buck power separation
- [x] Update images of new right angle picoblades
- [x] Update the assembly image of EPS2 and BAT4C
- [x] #125
- [x] #139

YanAzer, 2021-07-03:
@andrempmattos is there any other change done to v0.2 that i missed? if not i think this issue can be closed.

Closed 2021-08-03.

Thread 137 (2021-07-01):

Hardware: Remove ghost enable signal for OBDH regulator on MCU schematic

YanAzer, 2021-07-01:
This issue is not critical.

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

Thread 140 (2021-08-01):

Firmware: Develop a UART with interruption for handling TTC communication

andrempmattos, 2021-08-01:

mgm8, 2021-08-02:
Not only the TTC, but any device connected to the serial interface (UART port).

andrempmattos, 2021-08-02:
Yes, I developed a generic UART driver for communication with interruptions. I just need to improve the ISR routine part that curretly only works for USCI_A0 and inside it calls the param server task scheme (very specific to the TTC interface). If you have a better suggestion concerning this last part... otherwise I think for now I will let as it is, i. e., ISR should be added/modified for another use case.

Also, just an observation, in order to implement the isr inner routine more generically, I used the UART break char feature to flag the end of a communication, otherwise the EPS would not know the end of a package since the UART only has the RX interrupt flag for this purpose (different from I2C that has a stop bit flag).

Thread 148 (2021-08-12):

Firmware: Develop a unit test for the current sensor device

andrempmattos, 2021-08-12:
https://github.com/spacelab-ufsc/obdh2/blob/dev_firmware/firmware/tests/devices/current_sensor_test.c

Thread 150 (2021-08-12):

Firmware: Develop a unit test for the voltage sensor device

andrempmattos, 2021-08-12:
https://github.com/spacelab-ufsc/obdh2/blob/dev_firmware/firmware/tests/devices/voltage_sensor_test.c

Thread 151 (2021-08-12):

Firmware: Develop a unit test for the MPPT device

andrempmattos, 2021-08-12:
https://github.com/spacelab-ufsc/eps2/issues/141#issuecomment-891951157

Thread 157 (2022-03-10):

Firmware: Develop a driver for the DS2777G+ IC

mgm8, 2022-03-10:
This IC is similar to the [DS2775G+](https://github.com/spacelab-ufsc/eps2/tree/dev_firmware/firmware/drivers/ds2775g) from the old version of the EPS module, but instead of using a one-wire interface, it uses a more common I2C bus.

There is already a generic implementation that covers both types of interfaces: [https://github.com/spacelab-ufsc/eps2/tree/dev_firmware/firmware/drivers/ds277Xg](https://github.com/spacelab-ufsc/eps2/tree/dev_firmware/firmware/drivers/ds277Xg). This implementation must be improved, reviewed and tested.

* IC datasheet: [https://br.mouser.com/datasheet/2/256/DS2775-DS2778-1513647.pdf](https://br.mouser.com/datasheet/2/256/DS2775-DS2778-1513647.pdf)

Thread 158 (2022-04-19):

Hardware: Mount the missing PC-104 connector of the EM PCBs

mgm8, 2022-04-19:
One of the PC-104 connectors is missing on each PCB of the EM model.

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

Closed 2022-08-02.

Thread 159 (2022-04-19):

Hardware: Fix the battery header position

mgm8, 2022-04-19:
The battery connector of the EM model is mounted on the wrong side of the board (for the GOLDS-UFSC satellite, the battery module will be installed under the EPS board, so the battery connector must be on the bottom side of the board).

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

Closed 2022-08-02.

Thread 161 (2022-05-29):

Hardware: Evaluate the need of zener on DS2777G+ (Battery monitor IC) I2C bus

vinepb, 2022-05-29:
- IC datasheet: https://br.mouser.com/datasheet/2/256/DS2775-DS2778-1513647.pd

joaoclaudioeb, 2022-08-02:
If we want some extra protection, it is interesting to add Zener diodes to the I²C buses. But, it isn't necessary.

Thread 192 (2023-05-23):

Error loading new code in EPS2 V2.0

LucasAzulay, 2023-05-23:
We were using the EPS2 V1.0 but we changed to the EPS2 V2.0. When we tried to load the code in the new board this error appears.
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
We utilize the same device to load the code (Texas Instruments MSP-FET emulation tool) that used in the EPS2 V1.0.
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
The other boards are working as intended.

LucasAzulay, 2023-05-24:
We solved the problem. The jumper was missing in this place.
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

Closed 2023-05-24.

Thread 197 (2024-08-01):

I2C Communication

MatthewStueber, 2024-08-01:
I am trying to interface from an Arduino Uno (Master) with the EPS 2.0 board (Slave) via I2C. I have flashed the firmware, located on the spacelab-ufsc/eps2 GitHub page, to the EPS 2.0 MCU using the process highlighted in the README file located in the firmware folder. I have connected Dupont wires between the Arduino (A4 (SDA) and A5 (SCL)) to the ESP 2.0 (H2 pin 49 (SDA) and H2 pin 51 (SCL)) respectively. I understand that the Arduino must write an ID (0-48) to the EPS 2.0 then the ESP 2.0 will respond with the return of the ID. The Arduino Code is located below. The problem arises when the Arduino reads from the EPS 2.0. The data being read is different every time I request the Device ID which should return 0xEEE2 (The ID should not change). Please comment where I can find the correct way to interface via I2C, find the I2C packet structure or any suggested changes that should be made to the Arduino Code.

\\ Arduino Uno IDE code //
``` C++
#include <Wire.h>

#define EPS_I2C_ADDRESS 0x36  // EPS's I2C address
#define EPS2_PARAM_ID_DEVICE_ID 48  // Replace with the correct ID for EPS2_PARAM_ID_DEVICE_ID

void setup() {
  Wire.begin();  // Initialize I2C communication
  Serial.begin(9600);  // Initialize serial communication at 9600 baud

  // Writing the ID to the EPS
  uint32_t deviceID = 48;  // ID value you want to write

  for(int i=0; i<3; i++){
    Serial.println(" ");
    writeIDToEPS(EPS2_PARAM_ID_DEVICE_ID, deviceID);

    // Reading the ID back from the EPS
    uint32_t readID = readIDFromEPS(EPS2_PARAM_ID_DEVICE_ID);

    // Print the result to the Serial Monitor
    Serial.println(" ");
    Serial.print("Read Device ID: 0x");
    Serial.println(readID, HEX);
  }

}

void loop() {
  // Empty loop
}

void writeIDToEPS(uint8_t paramID, uint32_t value) {
  Wire.beginTransmission(EPS_I2C_ADDRESS);
  Wire.write(paramID);  // Send the parameter ID to EPS
  Wire.write((uint8_t*)&value, 4);  // Send the 32-bit value (4 bytes) to EPS
  //Wire.endTransmission();  // End transmission to EPS

  //delay(100);  // Small delay to ensure the EPS processes the command
}

uint32_t readIDFromEPS(uint8_t paramID) {
  Wire.beginTransmission(EPS_I2C_ADDRESS);
  Wire.write(paramID);  // Send the parameter ID to request data from EPS

  //delay(100);  // Small delay to allow the EPS to prepare the response

  Wire.requestFrom(EPS_I2C_ADDRESS, 4);  // Request 4 bytes (32-bit data) from EPS
  uint32_t value = 0;
  if (Wire.available() == 4) {
    uint8_t byte1 = Wire.read();
    uint8_t byte2 = Wire.read();
    uint8_t byte3 = Wire.read();
    uint8_t byte4 = Wire.read();

    // Print each byte received
    Serial.print("Received bytes: ");
    Serial.print(byte1, HEX); Serial.print(" ");
    Serial.print(byte2, HEX); Serial.print(" ");
    Serial.print(byte3, HEX); Serial.print(" ");
    Serial.println(byte4, HEX);

    value = byte4 | (byte3 << 8) | (byte2 << 16) | (byte1 << 24);
    //value = byte1 | (byte2 << 8) | (byte3 << 16) | (byte4 << 24)
  }
  Wire.endTransmission();  // End transmission to EPS
  //delay(100)

  return value;  // Return the 32-bit data read from EPS
}
```

\\ Serial Monitor Output //

Received bytes: 1 0 0 1

Read Device ID: 0x1

Received bytes: 9 F2 D4 40

Read Device ID: 0xFFFFD440

Received bytes: 4B EE 44 0

Read Device ID: 0x4400

joaoclaudioeb, 2024-08-02:
Hello, @MatthewStueber, how are you? I hope you're doing well! Based on your code, I am not sure if you are sending a data request in the correct format. In `firmware/devices/obdh/obdh.c`, you will notice that the EPS2 expects from the OBDH2 (or any other device trying to communicate with it via I²C) either a write request or a read request. In the case of a read request, as it seems to be the case here, it expects 2 bytes: the data to be read from its data structure and the CRC. Thus, the command you want to send in this case is `0x30 0x90`, with `0x90` being the CRC. The code below is found at [this link](https://github.com/spacelab-ufsc/eps2/blob/master/firmware/devices/obdh/obdh.c):

```c
int obdh_decode(uint8_t *adr, uint32_t *val, uint8_t *cmd)
{
    int err = 0;

    uint8_t buf[I2C_RX_BUFFER_MAX_SIZE] = {0};
    uint16_t received_size = 0;

    if (i2c_slave_read(buf, &received_size) == 0)
    {
        if (obdh_check_crc(buf, received_size - 1U, buf[received_size - 1U]) == true)
        {
            switch(received_size)
            {
                case OBDH_COMMAND_WRITE_SIZE:
                    *adr = buf[0];
                    *val = ((uint32_t)buf[1] << 24) |
                           ((uint32_t)buf[2] << 16) |
                           ((uint32_t)buf[3] << 8)  |
                           ((uint32_t)buf[4] << 0);
                    *cmd = OBDH_COMMAND_WRITE;

                    break;
                case OBDH_COMMAND_READ_SIZE:
                    *adr = buf[0];
                    *val = 0;
                    *cmd = OBDH_COMMAND_READ;

                    break;
                default:
                    sys_log_print_event_from_module(SYS_LOG_ERROR, OBDH_MODULE_NAME, "Invalid command received (CMD)!");
                    sys_log_new_line();

                    err = -1;

                    break;
            }
        }
        else
        {
            sys_log_print_event_from_module(SYS_LOG_ERROR, OBDH_MODULE_NAME, "Invalid command received (CRC)!");
            sys_log_new_line();

            err = -1;
        }
    }
    else
    {
        err = -1;
    }

    return err;
}
```

Additionally, the EPS2 will respond with 6 bytes. In this specific case, it will respond `0x30 0x00 0x00 0xEE 0xE2 0x63`, with `0x63` being the CRC of the message. Could you check your sending and receiving functions to confirm that the message being sent is correct and that the reception is in accordance with this format?

MatthewStueber, 2024-08-02:
Hi @joaoclaudioeb, I am doing great! Thank you for your response, and I appreciate the detailed explanation regarding the I2C protocol. After reviewing your informative message I have corrected my Arduino code. The code now uses the correct format for sending and receiving functions, and the EPS 2.0 responds as specified.  Below is the corrected code and Serial Monitor output.

``` C++
/*
  This code is used with the SpaceLab EPS 2.0.
  The code will send a read command to the EPS.
  The command is 2 bytes: the first byte is the ID, followed by a
  Cyclic Redundancy Check (CRC). This code sends the ID
  of 48 which is 0x30 in Hex. The EPS then responds with
  6 bytes of data. The response structure is as follows:
  it begins with the requested ID, followed by 2 padding bytes
  of 0x00. The last two bytes contain the requested data, for this
  code it is the Device ID (0xEEE2). The response concludes with the
  CRC byte verification.
*/

#include <Wire.h>

#define EPS_I2C_ADDRESS 0x36  // EPS's I2C address
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
MatthewStueber, 2024-08-12:
Hi @joaoclaudioeb,

Thank you for your guidance. I’ve updated the firmware by setting ADC_VREF_V to 3.3 and ADC_VREF_MV to 3300UL, as you suggested. I verified the reference voltage on the EPS PCB and found it to be approximately 2.678V, which aligns well with the 3.3V setting.

The ADC returns are now more accurate, but there are still some discrepancies compared to what I was expecting. Below are the latest outputs:
``` C
debian@BeagleBone:~/EPS$ ./a.out
 0x0 0x0 0x0 0x8 0xE6 0x14
 0x1 0x0 0x0 0x0 0x0 0x62
 0x2 0x0 0x0 0x0 0x2D 0x7
 0x3 0x0 0x0 0x0 0x2 0xA8
 0x4 0x0 0x0 0x0 0x0 0x8F
 0xE 0x0 0x0 0x0 0x32 0xCC
 0xF 0x0 0x0 0x0 0x32 0xAE
 0x10 0x0 0x0 0x0 0x32 0xAC
 0x12 0x0 0x0 0x1D 0x9 0x77
 0x29 0x0 0x0 0x0 0x0 0x1F
 0x2A 0x0 0x0 0x0 0x0 0xB9
 0x2B 0x0 0x0 0x0 0x0 0xDB
 0x2C 0x0 0x0 0x0 0x0 0xF2
 0x2D 0x0 0x0 0x0 0x0 0x90
 0x30 0x0 0x0 0xEE 0xE2 0x63
debian@BeagleBone:~/EPS$ ./a.out
 0x0 0x0 0x1 0xDD 0xA6 0x43
 0x1 0x0 0x0 0x0 0x0 0x62
 0x2 0x0 0x0 0x0 0x2D 0x7
 0x3 0x0 0x0 0x0 0x2 0xA8
 0x4 0x0 0x0 0x0 0x0 0x8F
 0xE 0x0 0x0 0x0 0x32 0xCC
 0xF 0x0 0x0 0x0 0x32 0xAE
 0x10 0x0 0x0 0x0 0x32 0xAC
 0x12 0x0 0x0 0x1D 0xC 0x6C
 0x29 0x0 0x0 0x0 0x0 0x1F
 0x2A 0x0 0x0 0x0 0x0 0xB9
 0x2B 0x0 0x0 0x0 0x0 0xDB
 0x2C 0x0 0x0 0x0 0x0 0xF2
 0x2D 0x0 0x0 0x0 0x0 0x90
 0x30 0x0 0x0 0xEE 0xE2 0x63
debian@BeagleBone:~/EPS$

```
As shown, the current and voltage readings are still slightly off, and the hardware/firmware version values are not coming through correctly. Additionally, the temperature reading from the microcontroller is still returning zeros. Could you advise on other adjustments that might be needed? Should I make the rest of the the changes in the fix/eps-data-structure/#197?  Also, I am curious about the counter command: does it involve the watchdog timer, or is it controlled differently? I appreciate your continued support and look forward to your insights.
Thank you!

joaoclaudioeb, 2024-08-13:
Hi, @MatthewStueber, could you clarify a few things?

1) Are you using the EPS to power something? The data from ID `0x02` (`EPS2_PARAM_ID_EPS_CURRENT`) is related to the current from the 3.3V converter in the EPS, which usually powers some internal EPS circuits and the TTC. So, you won't see the 64mA from the power supply in this data; you'll see something slightly lower. The 64mA will appear in the data from ID `0x1B` (`EPS2_PARAM_ID_BAT_CURRENT`), which is related to the current drawn from the battery. Some circuits are directly connected to the VBUS (e.g., converters, battery monitor), while others are connected to the output of the 3.3V converter. This explains the difference in readings. However, converting the current you read in HEX, it seems something else might be drawing from the 3.3V bus. Can you confirm this?

2) The VBUS voltage reading from ID `0x18` (`EPS2_PARAM_ID_SP_MZ_CURRENT`) seems relatively accurate, assuming you're powering the EPS with 7.4V and 3.7V (for reference). Can you confirm this?

Furthermore, no need to touch the fix/eps-data-structure/#197 branch; I'll be making corrections today and tomorrow. The MCU temperature and possibly some other measurements aren't being updated in the data structure, which is why you're seeing zero values. This is a simple fix. However, if you're seeing strange values in the updated readings, it might be because negative numbers are being sent as uint16 instead of int16. I'll correct these details and check if there are any other odd values being sent.

Thank you for your patience and interest in our platform! If you'd like, feel free to share more about your project and goals with us — we'd love to hear about it! I'll let you know as soon as I make the changes in the new branch. Talk soon!

MatthewStueber, 2024-08-13:
Hi @joaoclaudioeb,

Thank you for your prompt clarification. I’ve been testing with the EPS without any load attached, powering it through the battery connector with the 3.7V and 7.4V sources as outlined in the documentation. I’ve confirmed the register returns with a BeagleBone Black connected via the 3.3V I2C data lines. I appreciate the reasoning behind changing the uint16 to int16 and look forward to seeing the updates.

I’m currently working with my team on designing a 3U CubeSat, using the BeagleBone Black as the OBC and the SpaceLab EPS 2.0 to better understand typical CubeSat electrical power subsystem designs. While the EPS is fabricated, we don’t have the BAT4C battery module. Our end goal is to establish a complete test setup with the SpaceLab EPS 2.0, a solar array emulator, and a spacecraft load emulator.

Regarding the solar array emulator, I’ve been trying to power the EPS through three of the six solar array connectors. Currently, with the power supply set to 7V and 800mA connected to the -Y,
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

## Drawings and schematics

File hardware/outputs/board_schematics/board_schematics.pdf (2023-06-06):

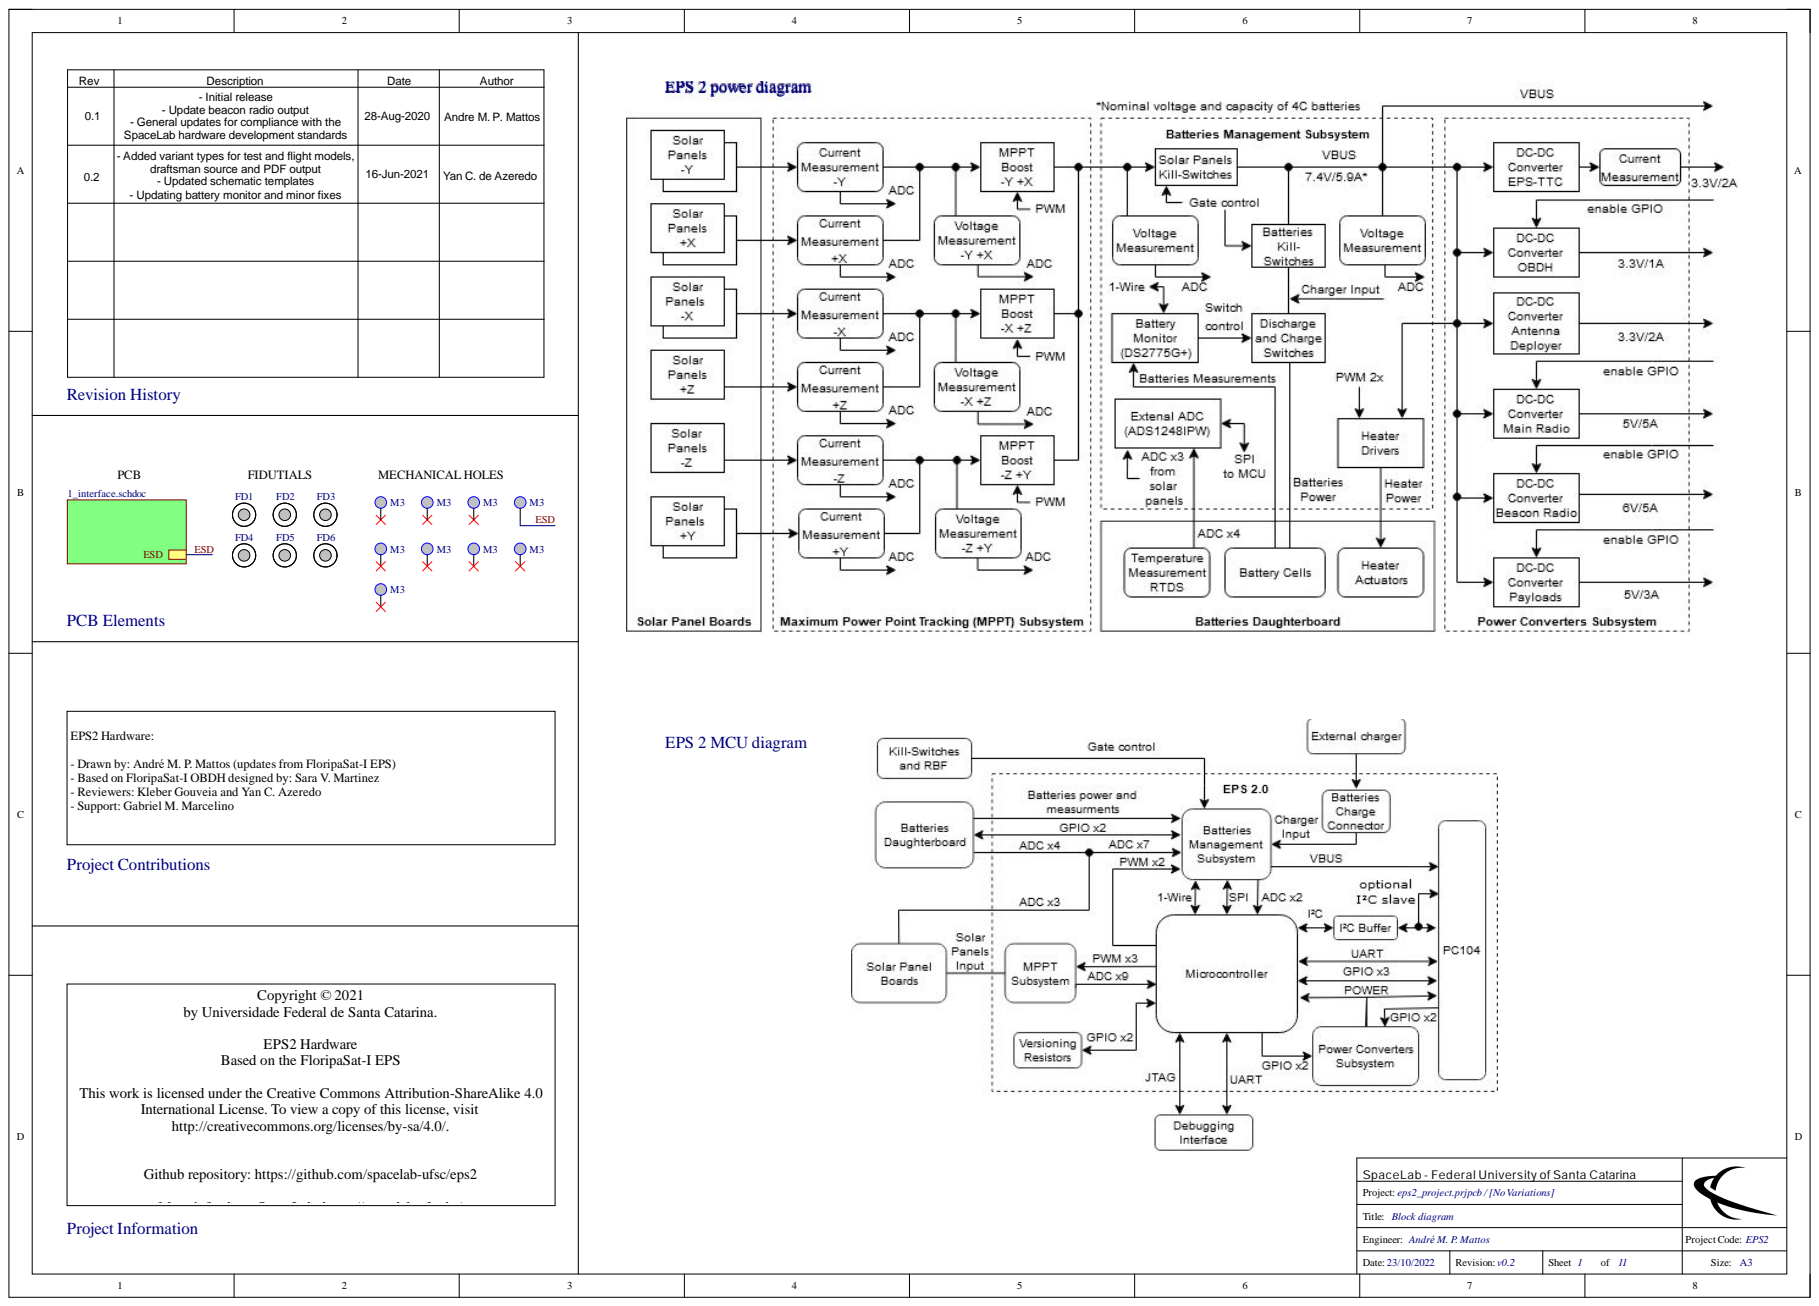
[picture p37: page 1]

EPS 2 power diagram EPS 2 MCU diagram

Re v | Descriptio n | Date | A uth o r
0.1 | - Initial r ele ase - Up d ate b e aco n r a dio o utp u t - Ge n e r al u p d ates fo r co m plia nce with th e S p ace L a b h a r dwa r e d evelo p m e nt sta n d a r d s | 2 8 -A u g -2 0 2 0 | A n d r e M. P. M atto s

0.2 | -A d d e d va ria nt typ es fo r test a n d flig ht m o d els, d r aftsm a n so u rce a n d PDF o utp u t - Up d ate d sch e m atic te m plate s - Up d atin g b atte ry m o nito r a n d min o r fixe s | 1 6 -Ju n -2 0 2 1 | Ya n C. d e Aze r e d o

ased on the Floripa

This work is lic

To view a copy of this lic
commons.org/lic

epository: https://github.com/spa

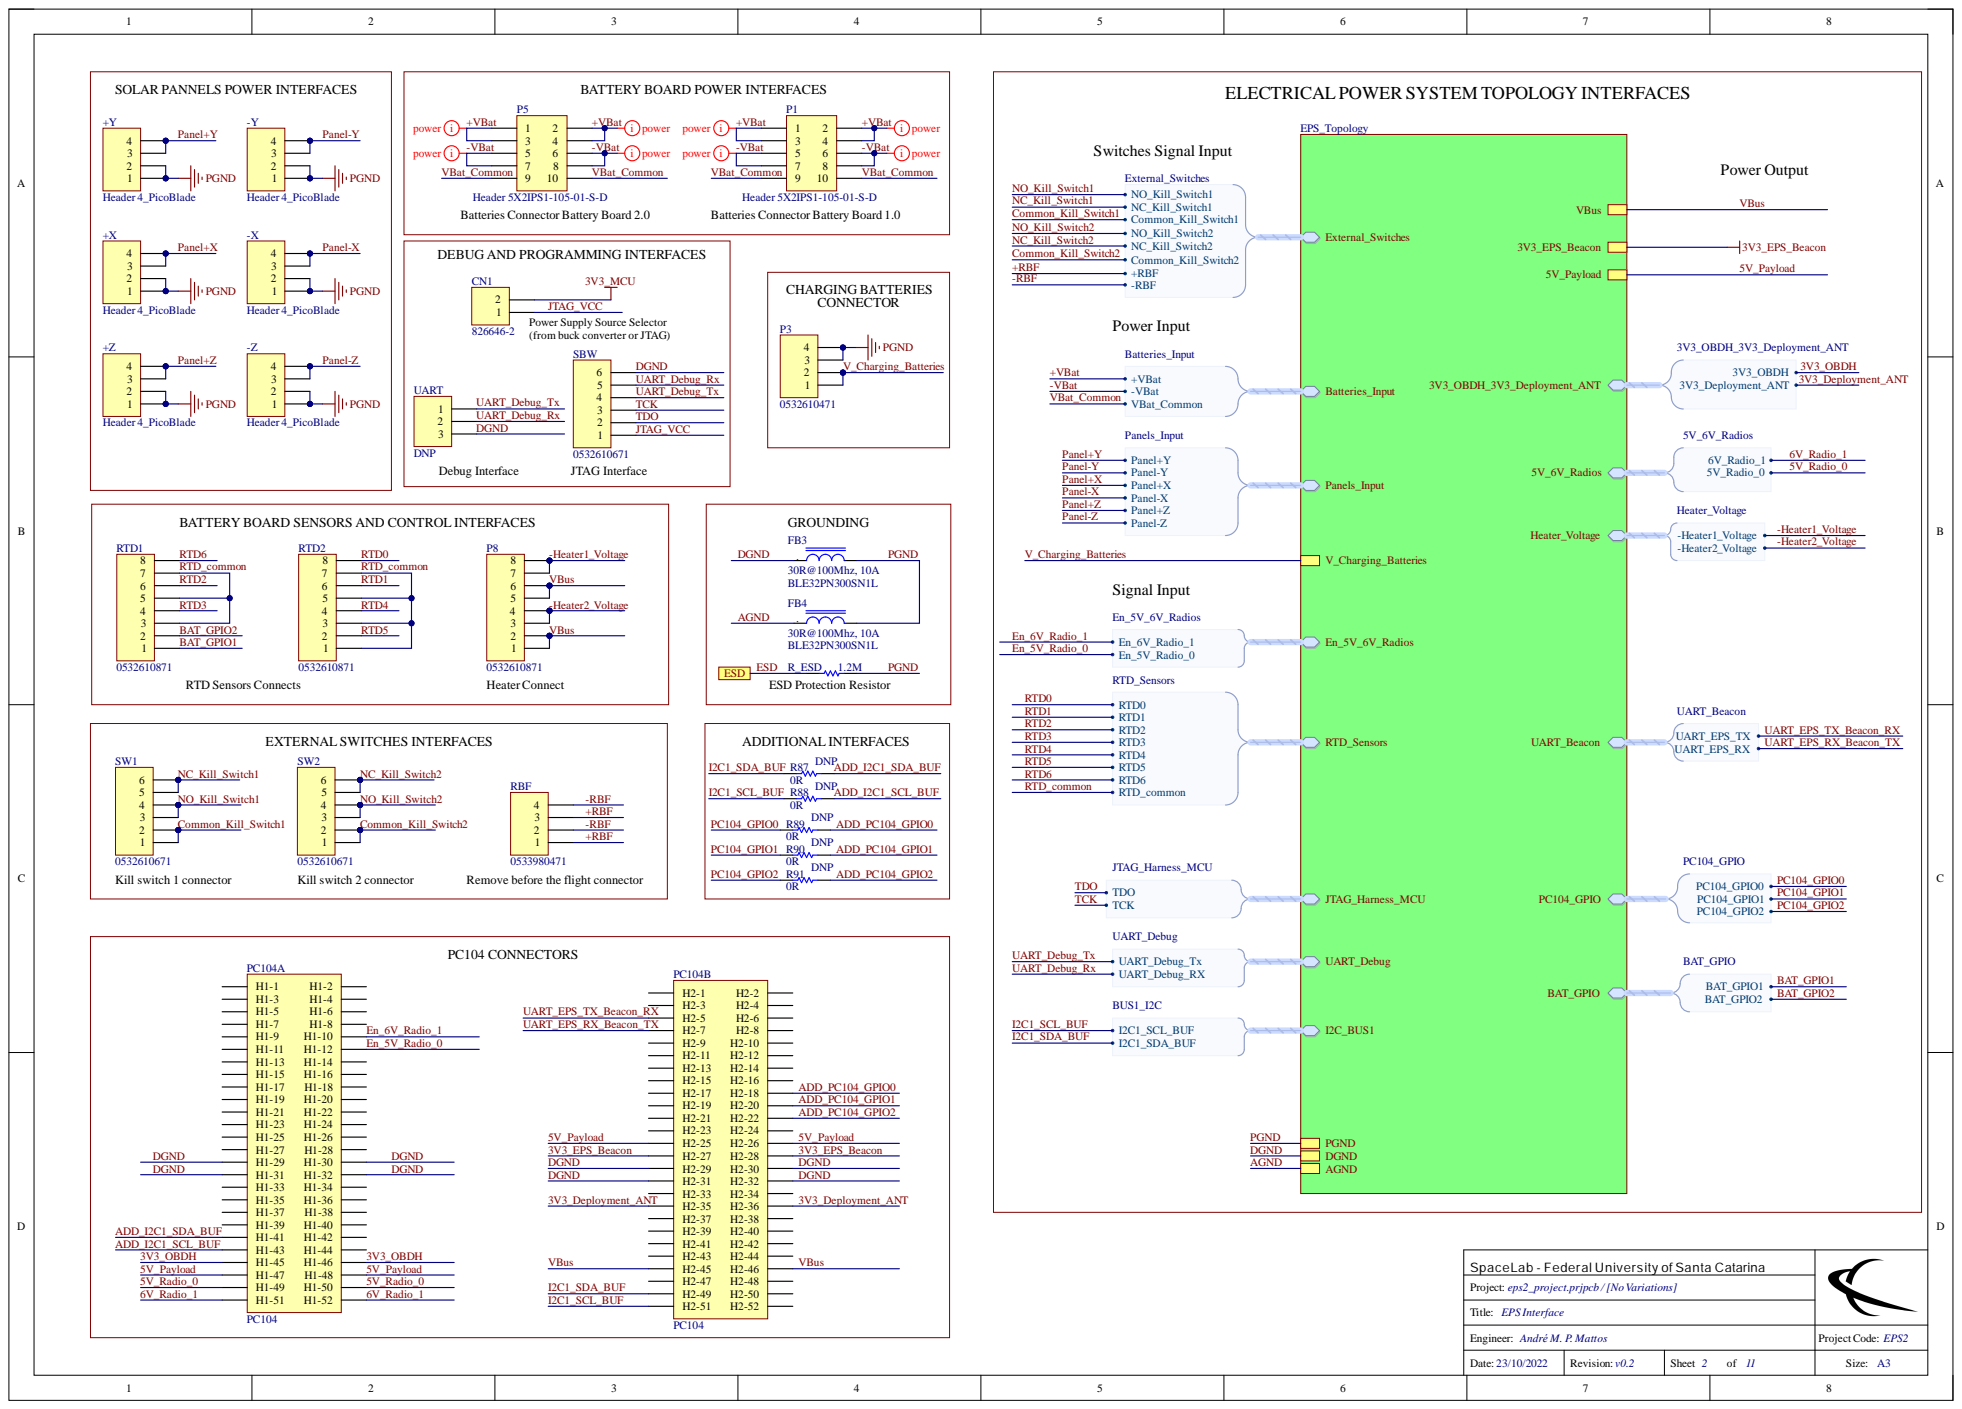
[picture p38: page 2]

SOLAR PANNELS POWER INTERFACES

BATTERY BOARD POWER INTERFACES

ELECTRICAL POWER SYSTEM TOPOLOGY INTERFACES

Header 5X2IPS1-105-01-S-D
Batteries Connector Battery Board 2.0

Batteries Connector Battery Board 1.0

DEBUG AND PROGRAMMING INTERFACES

JTAG_VCC
Power Supply Source Selector
(from buck converter or JTAG)

UART_Debug_Rx | TDO
DGND | JTAG_VCC

BATTERY BOARD SENSORS AND CONTROL INTERFACES

Remove before the flight connector

SpaceLab - Federal University of Santa Catarina

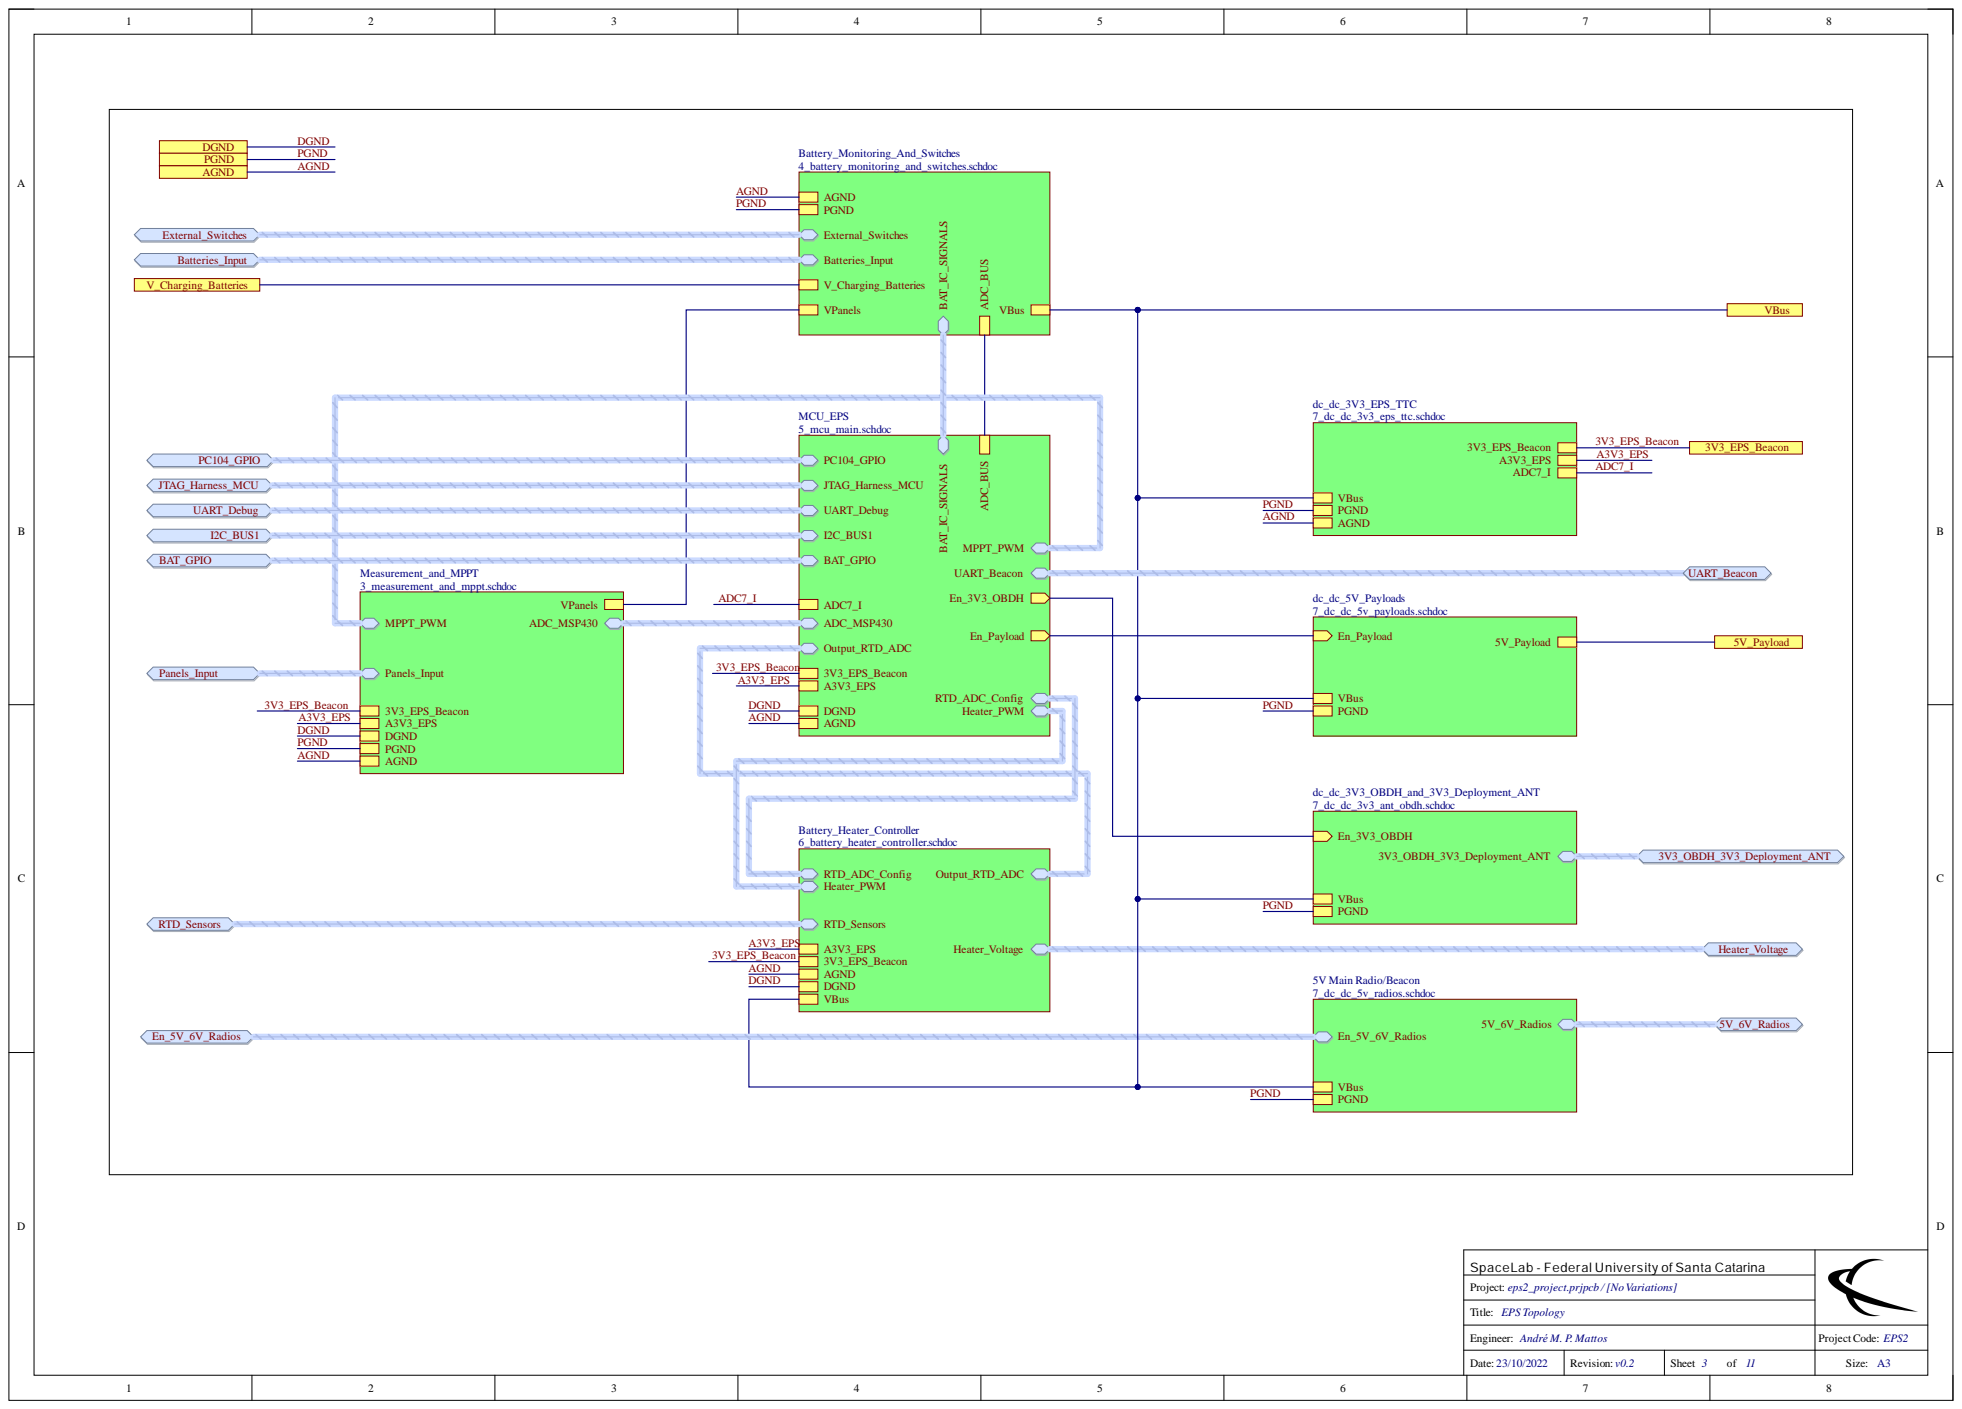
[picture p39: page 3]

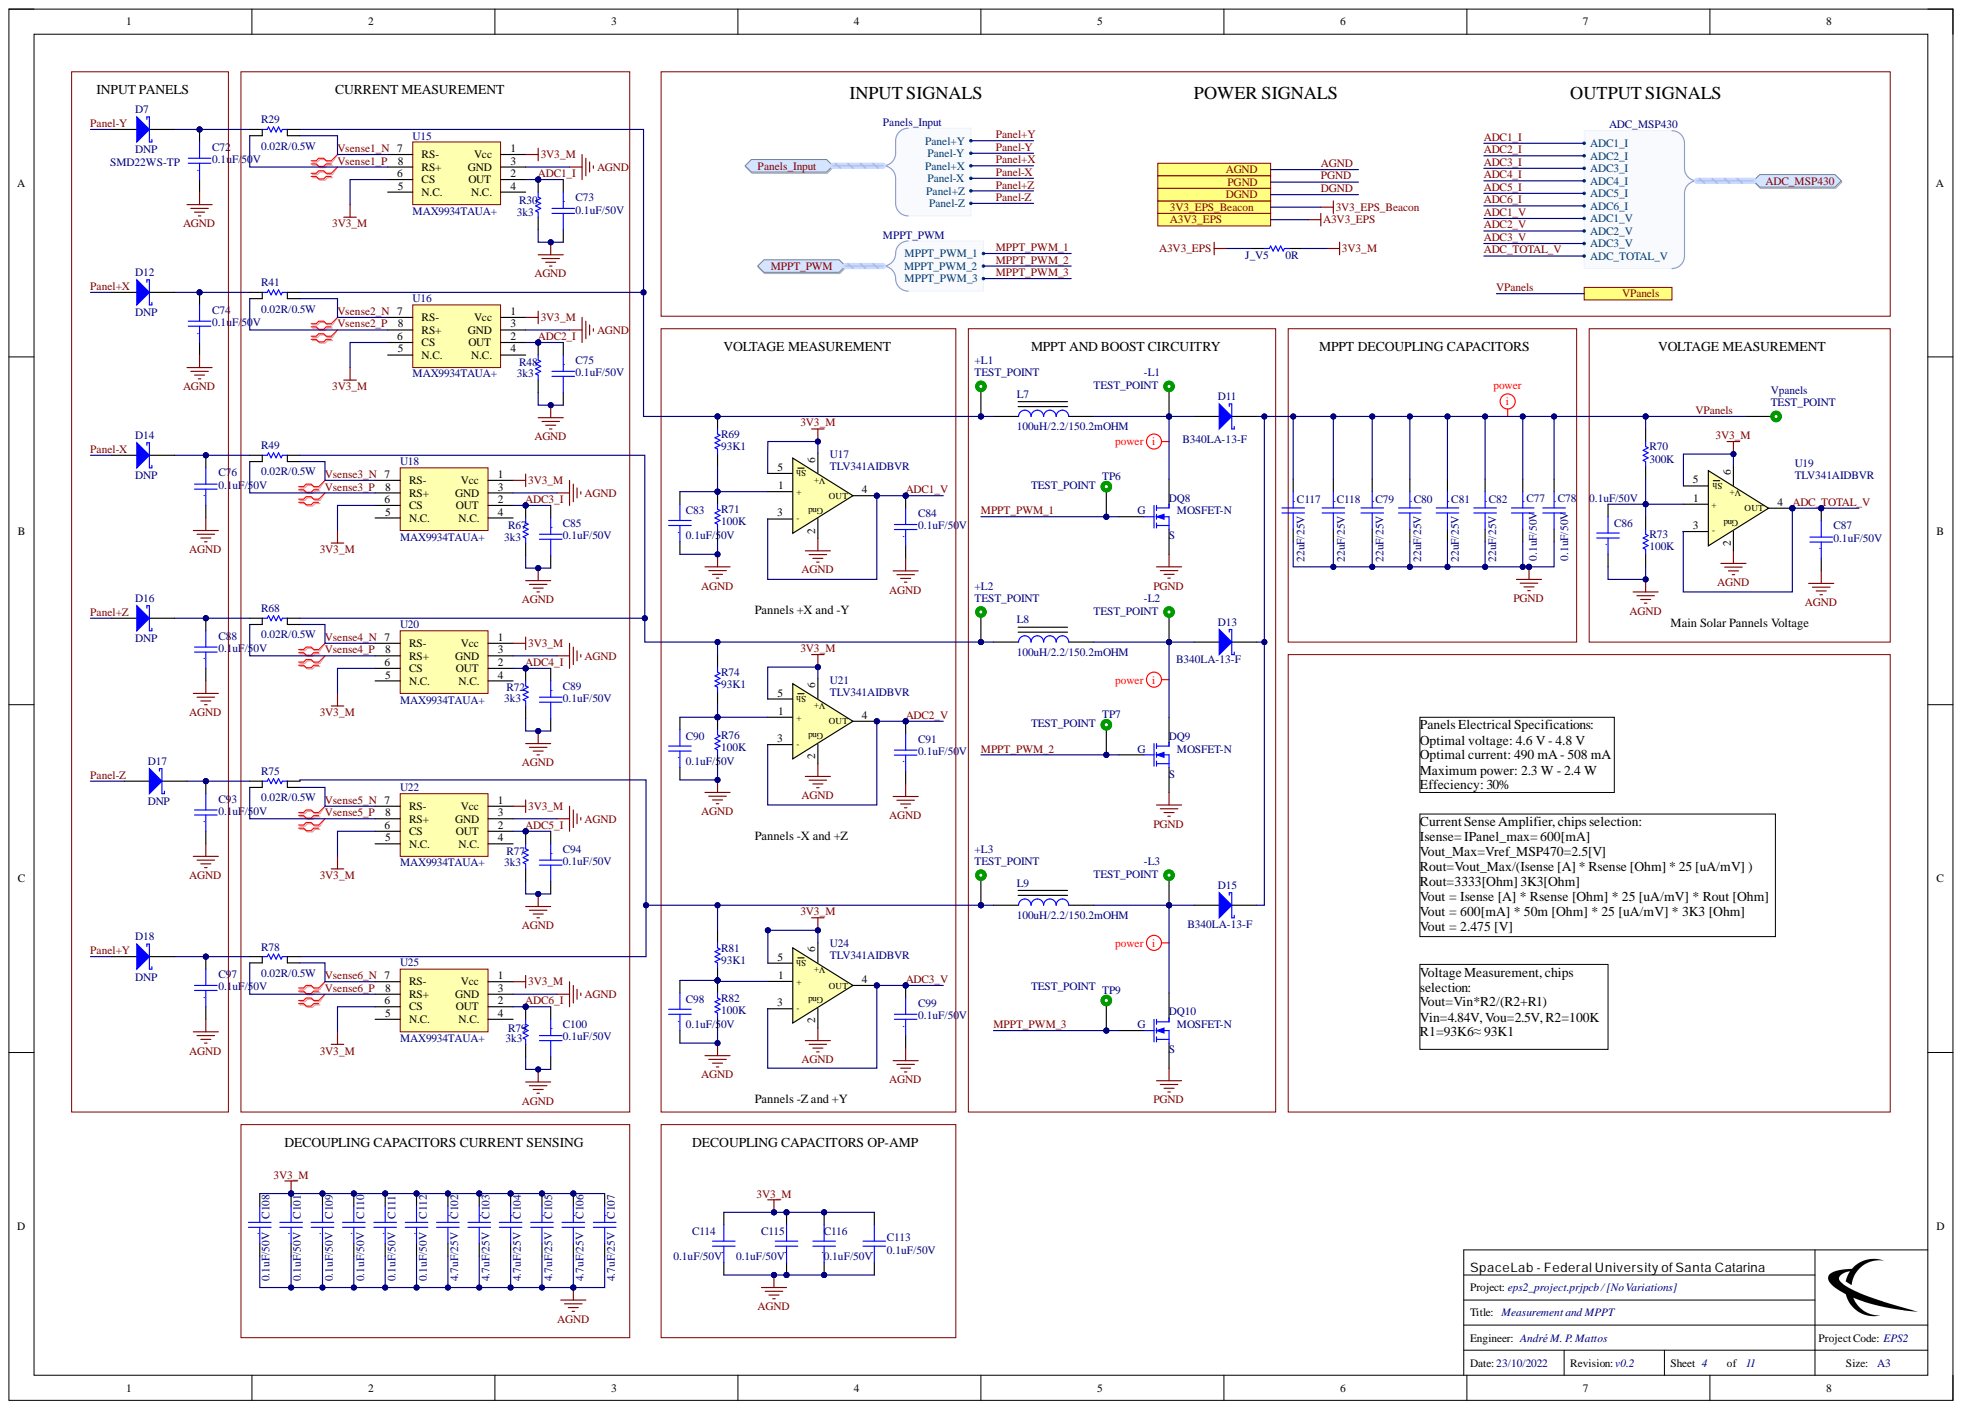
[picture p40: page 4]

D17 | 0.02R/0.5W | Vsense4_N | U20

Main Solar Pannels Voltage

PanelsElectrical Specifications:
Optimal voltage: 4.6 V - 4.8 V
Optimal current: 490 mA - 508 mA
Maximum power: 2.3 W - 2.4 W
Effeciency: 30%

Current Sense Amplifier, chipsselection:
Isense= IPanel_max= 600[mA]
Vout_Max=Vref_MSP470=2.5[V]
Rout=Vout_Max/(Isense [A] * Rsense [Ohm] * 25 [uA/mV] )
Rout=3333[Ohm] 3K3[Ohm]
Vout = Isense [A] * Rsense [Ohm] * 25 [uA/mV] * Rout [Ohm]
Vout = 600[mA] * 50m [Ohm] * 25 [uA/mV] * 3K3 [Ohm]
Vout = 2.475 [V]

SpaceLab - Federal University of Santa Catarina

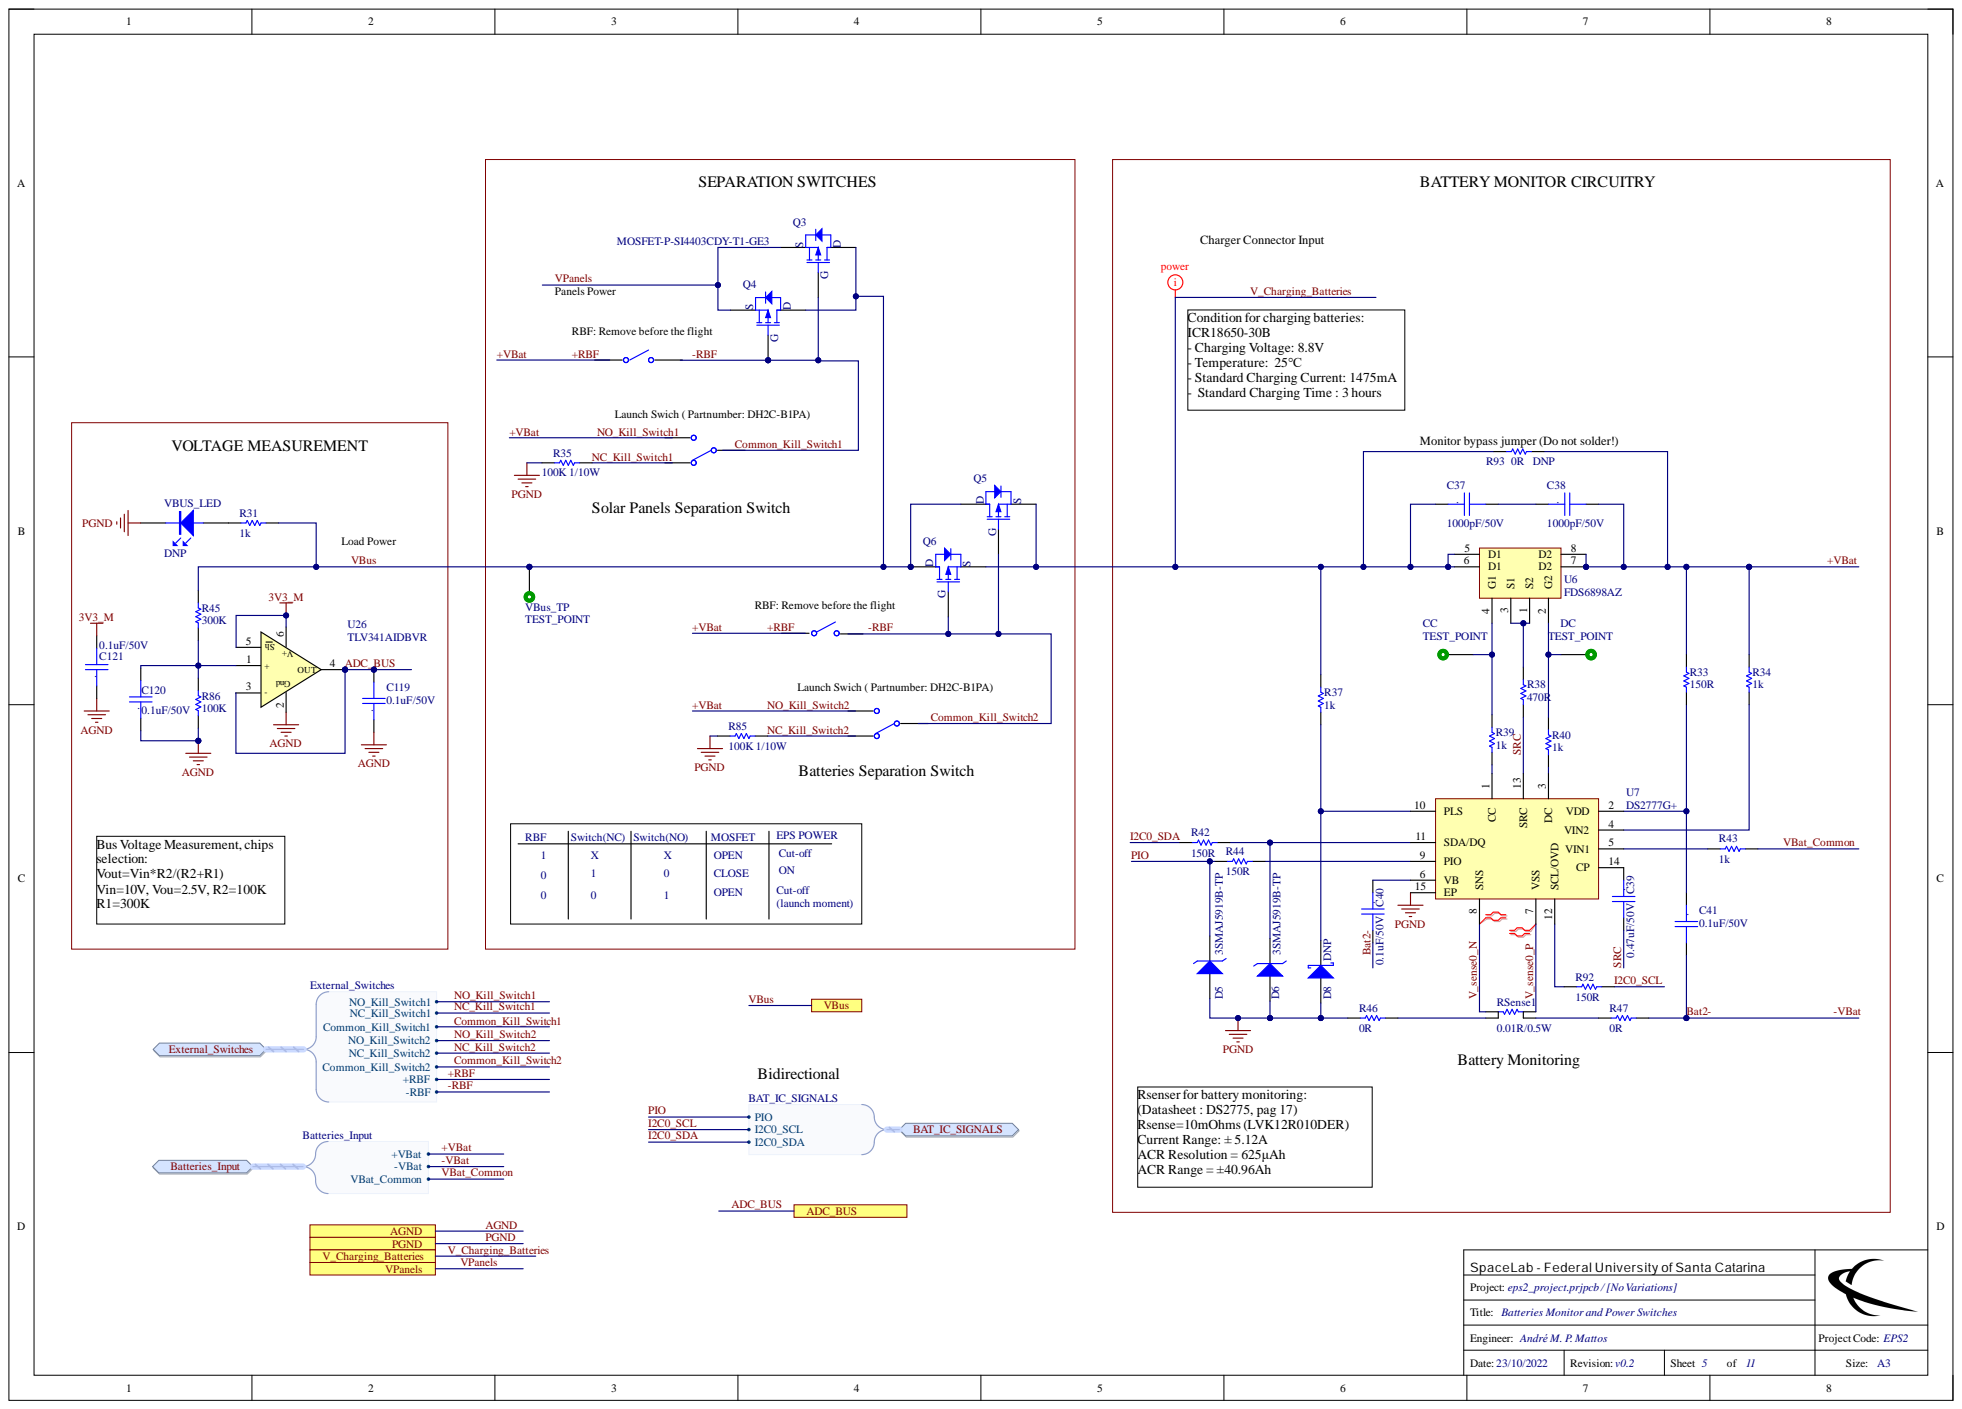
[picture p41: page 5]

RBF: Remove before the flight

Condition for charging batteries:
ICR18650-30B
- Charging Voltage: 8.8V
- Temperature: 25℃
- Standard Charging Current: 1475mA
- Standard Charging Time : 3 hours

Solar Panels Separation Switch

SDA/DQ 11

Rsenser for battery monitoring:
(Datasheet : DS2775, pag 17)
Rsense=10mOhms(LVK12R010DER)
Current Range: ± 5.12A
ACR Resolution = 625μAh
ACR Range = ±40.96Ah

SpaceLab - Federal University of Santa Catarina

Batteries Monitor and Power Switches
Title:

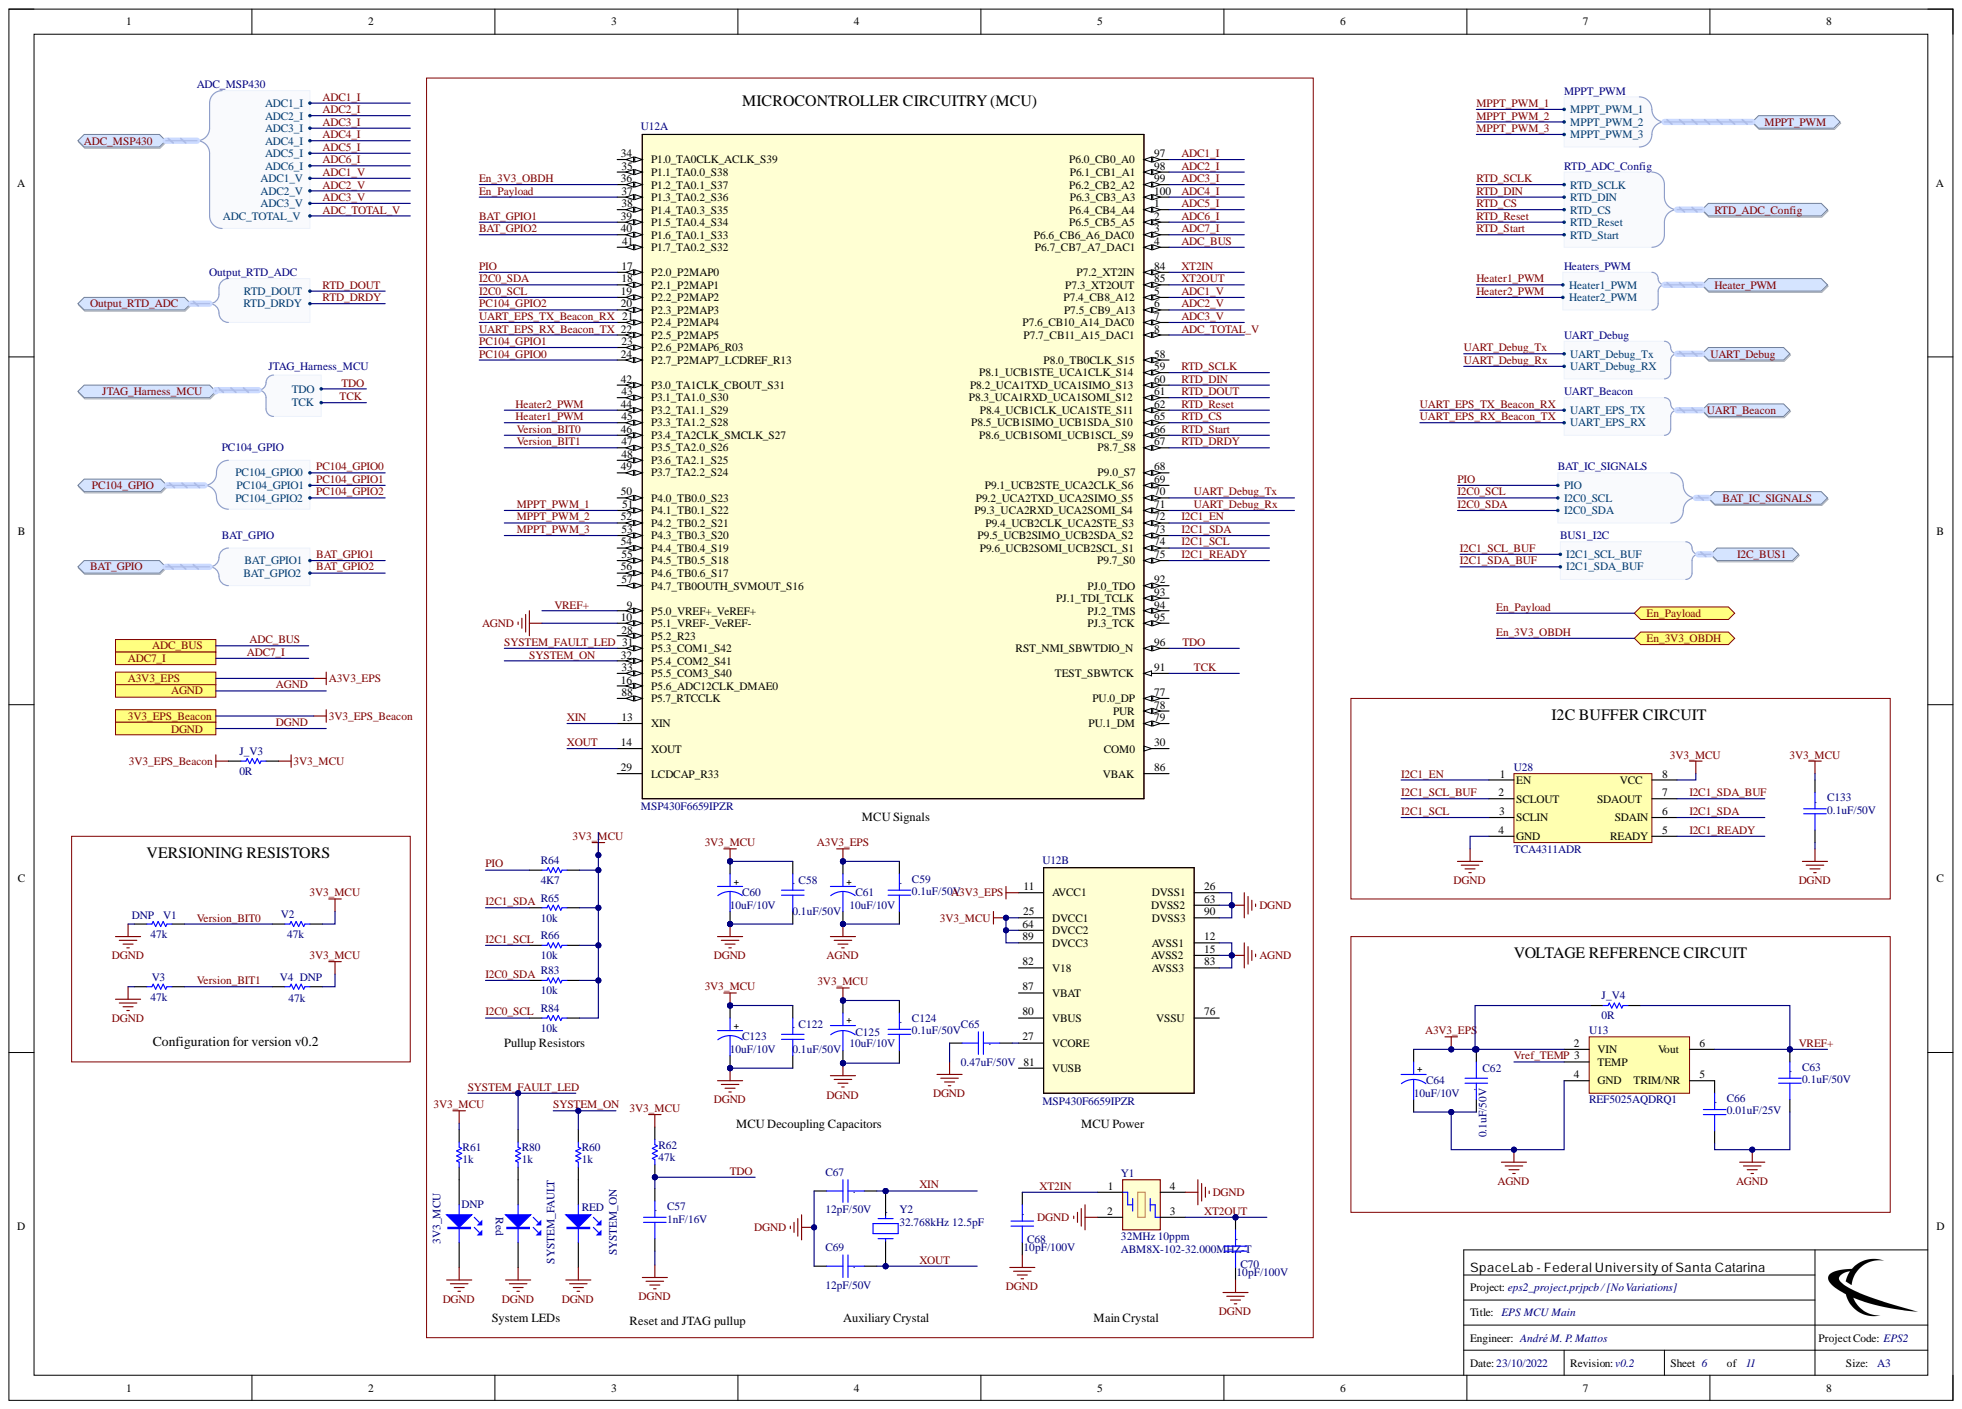
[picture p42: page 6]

SpaceLab - Federal University of Santa Catarina

Reset and JTAG pullup

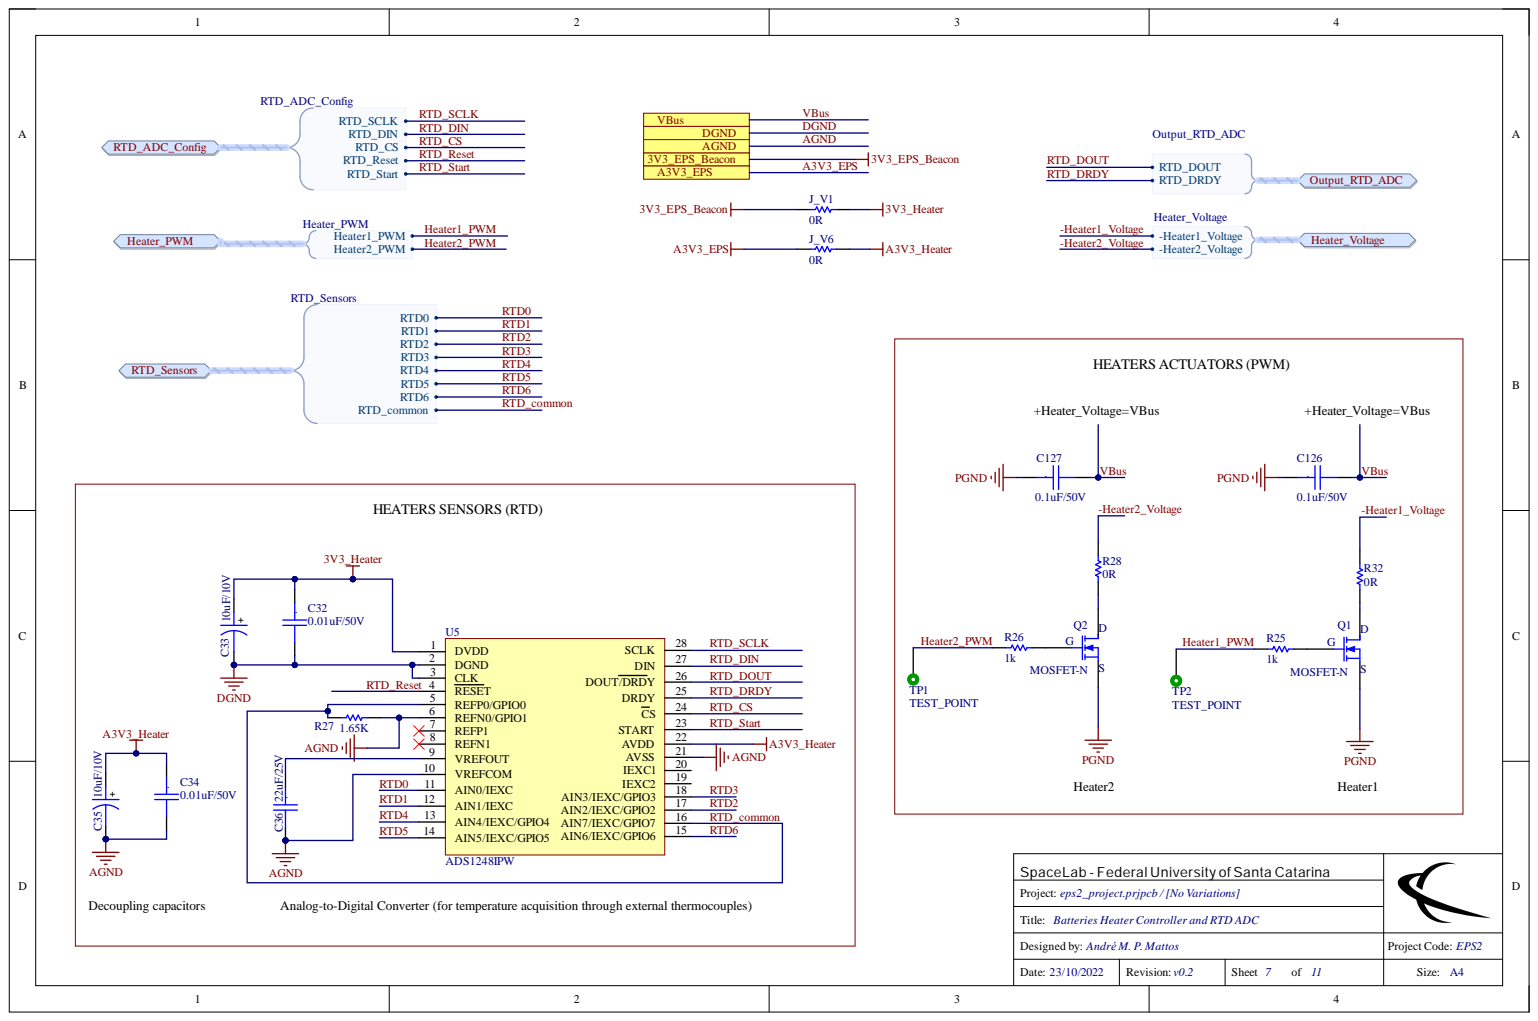
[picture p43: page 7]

REFP0/GPIO0 5

REFP1 7

VREFOUT 9 | RTD3 RTD_common

RTD0 . RTD1 RTD4 RTD5 | | AIN0/IEXC 11 AIN1/IEXC 12 AIN4/IEXC/GPIO4 13

SpaceLab - Federal University of Santa Catarina

Batteries Heater Controller and RTD ADC

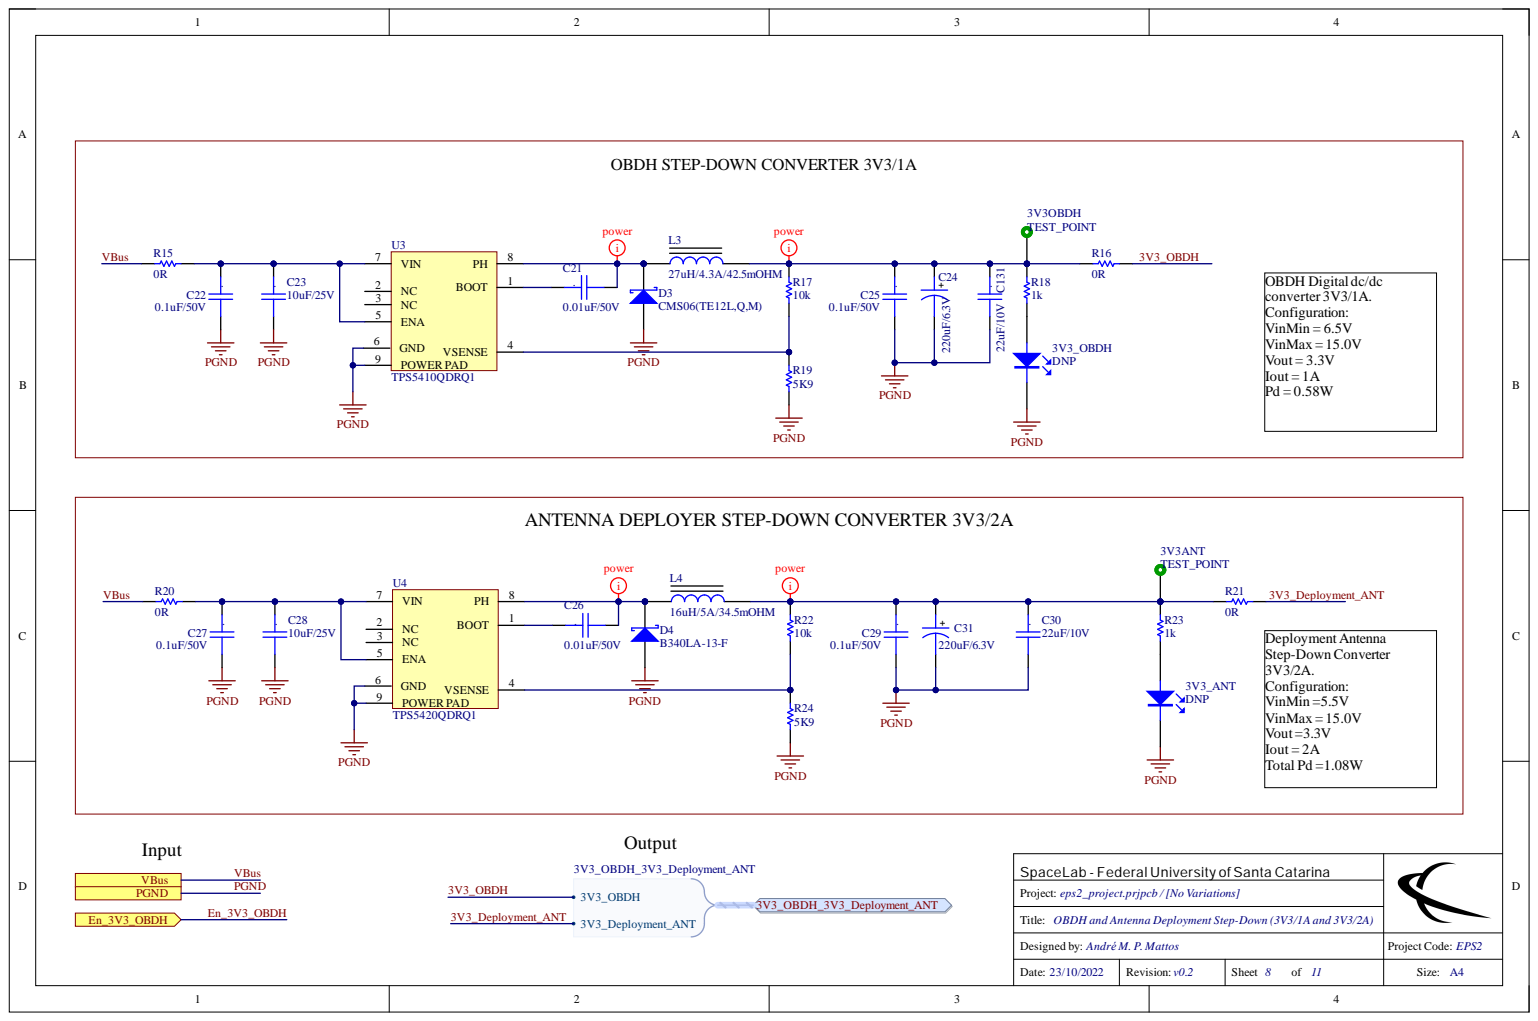
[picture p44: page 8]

OBDH STEP-DOWN CONVERTER 3V3/1A

ANTENNA DEPLOYER STEP-DOWN CONVERTER 3V3/2A

SpaceLab - Federal University of Santa Catarina

OBDH and Antenna Deployment Step-Down (3V3/1A and 3V3/2A)

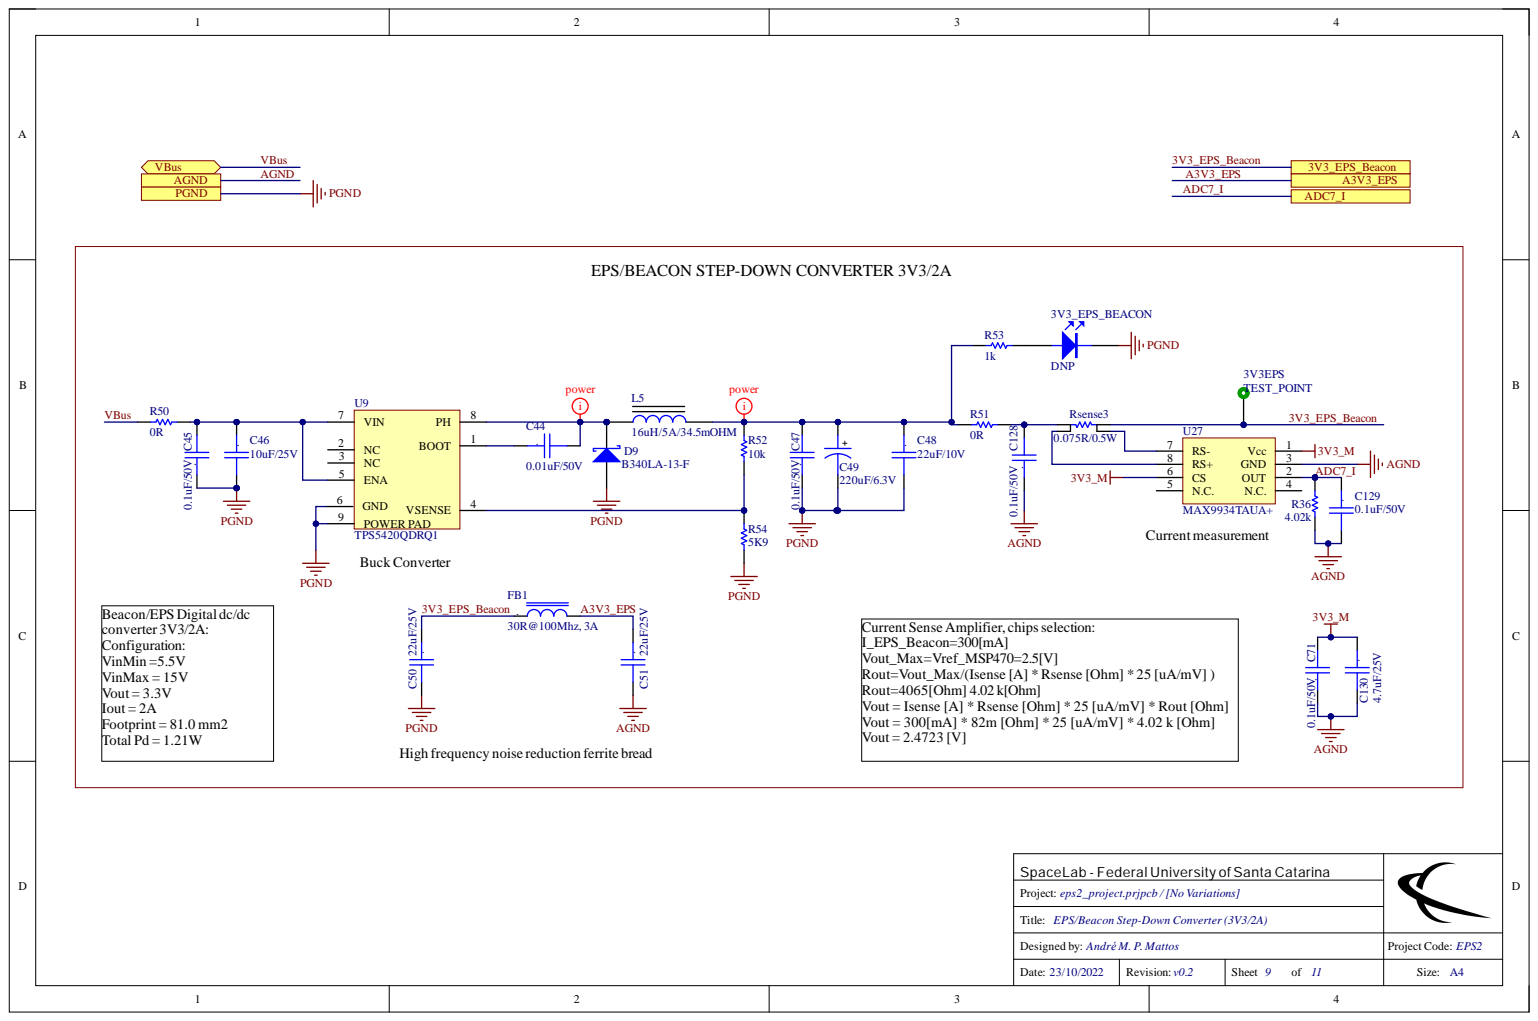
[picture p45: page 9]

EPS/BEACON STEP-DOWN CONVERTER 3V3/2A

Current Sense Amplifier, chips selection:
I_EPS_Beacon=300[mA]
Vout_Max=Vref_MSP470=2.5[V]
Rout=Vout_Max/(Isense [A] *Rsense [Ohm] * 25 [uA/mV] )
Rout=4065[Ohm] 4.02 k[Ohm]
Vout = Isense [A] * Rsense [Ohm] * 25 [uA/mV] * Rout [Ohm]
Vout = 300[mA] * 82m [Ohm] * 25 [uA/mV] * 4.02 k [Ohm]
Vout = 2.4723 [V]

High frequency noise reduction ferrite bread

SpaceLab - Federal University of Santa Catarina

EPS/Beacon Step-Down Converter (3V3/2A)

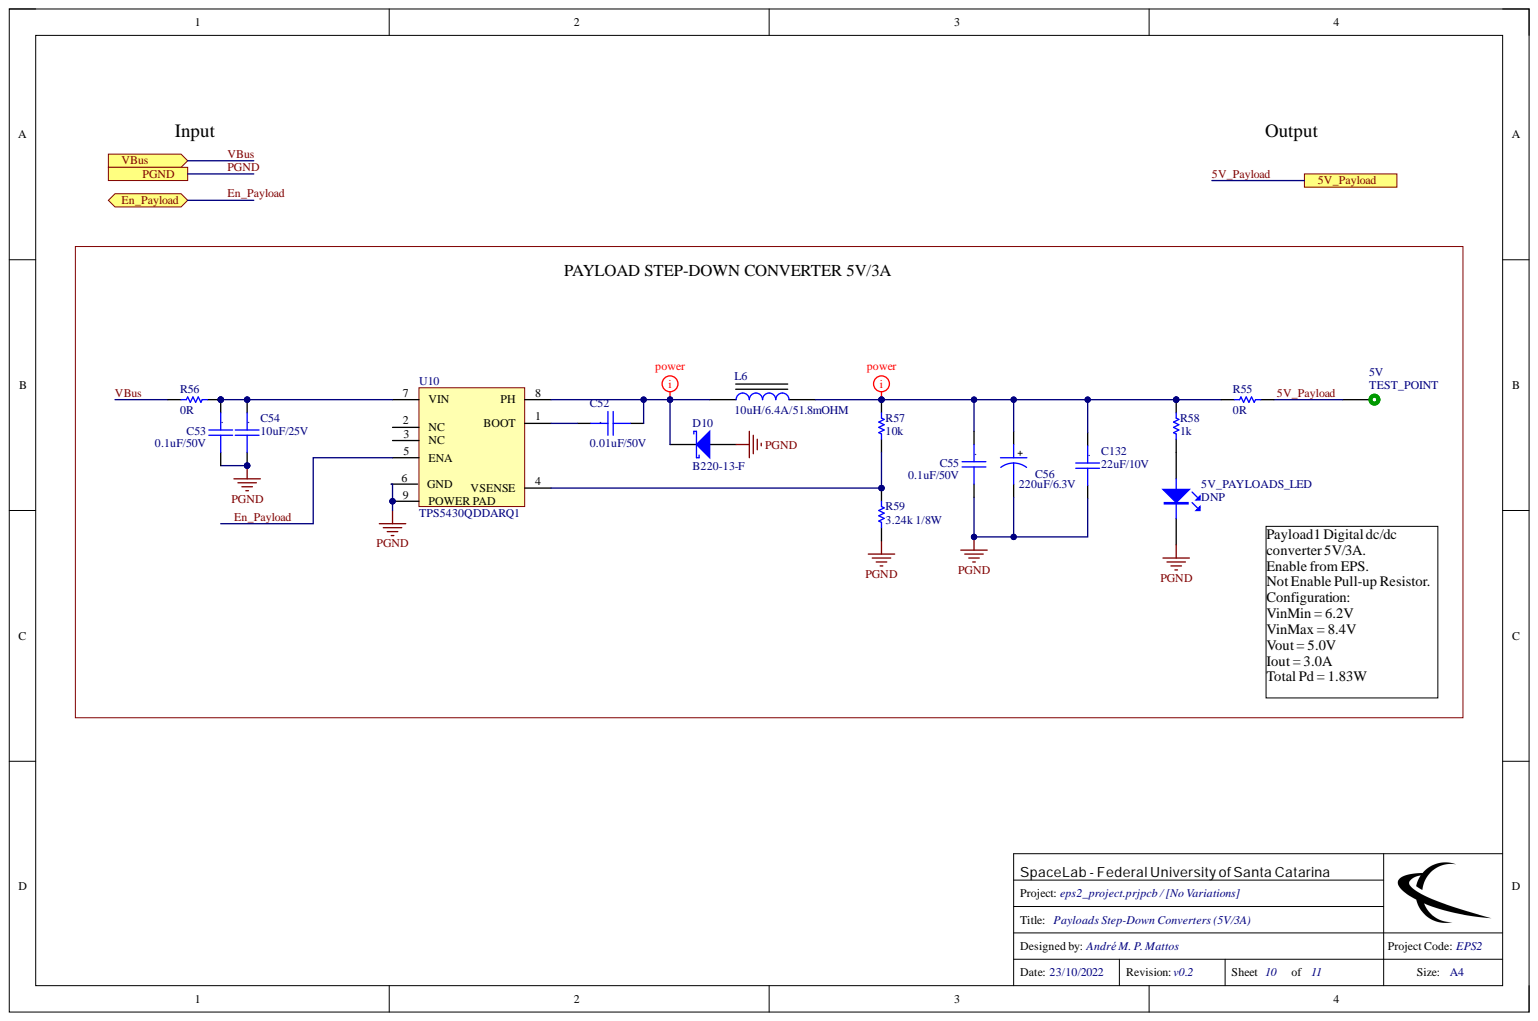
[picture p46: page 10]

PAYLOAD STEP-DOWN CONVERTER 5V/3A

SpaceLab - Federal University of Santa Catarina

Payloads Step-Down Converters (5V/3A)

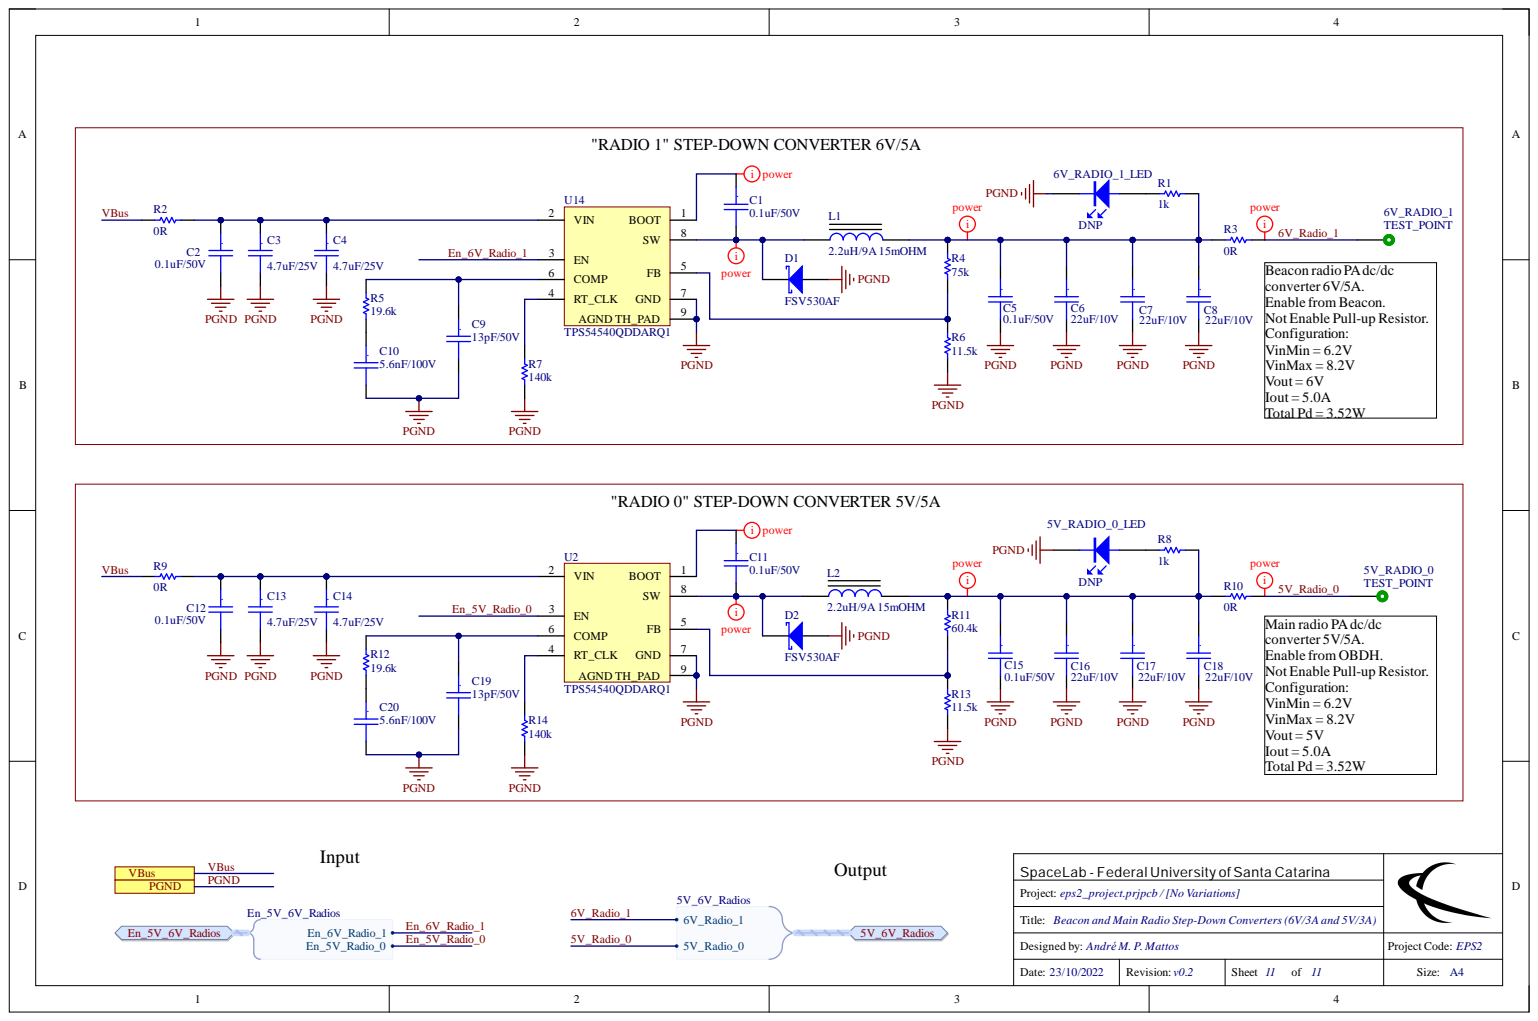
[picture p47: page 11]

"RADIO 1" STEP-DOWN CONVERTER 6V/5A

Beacon radio PAdc/dc
converter 6V/5A.
Enable from Beacon.
Not Enable Pull-up Resistor.
Configuration:
VinMin = 6.2V
VinMax = 8.2V
Vout = 6V
Iout = 5.0A
Total Pd = 3.52W

"RADIO 0" STEP-DOWN CONVERTER 5V/5A | 5V_RADIO_0_LED

Main radio PAdc/dc
converter 5V/5A.
Enable from OBDH.
Vout = 5V

RT_CLK 4

SpaceLab - Federal University of Santa Catarina

Beacon and Main Radio Step-Down Converters (6V/3A and 5V/3A)

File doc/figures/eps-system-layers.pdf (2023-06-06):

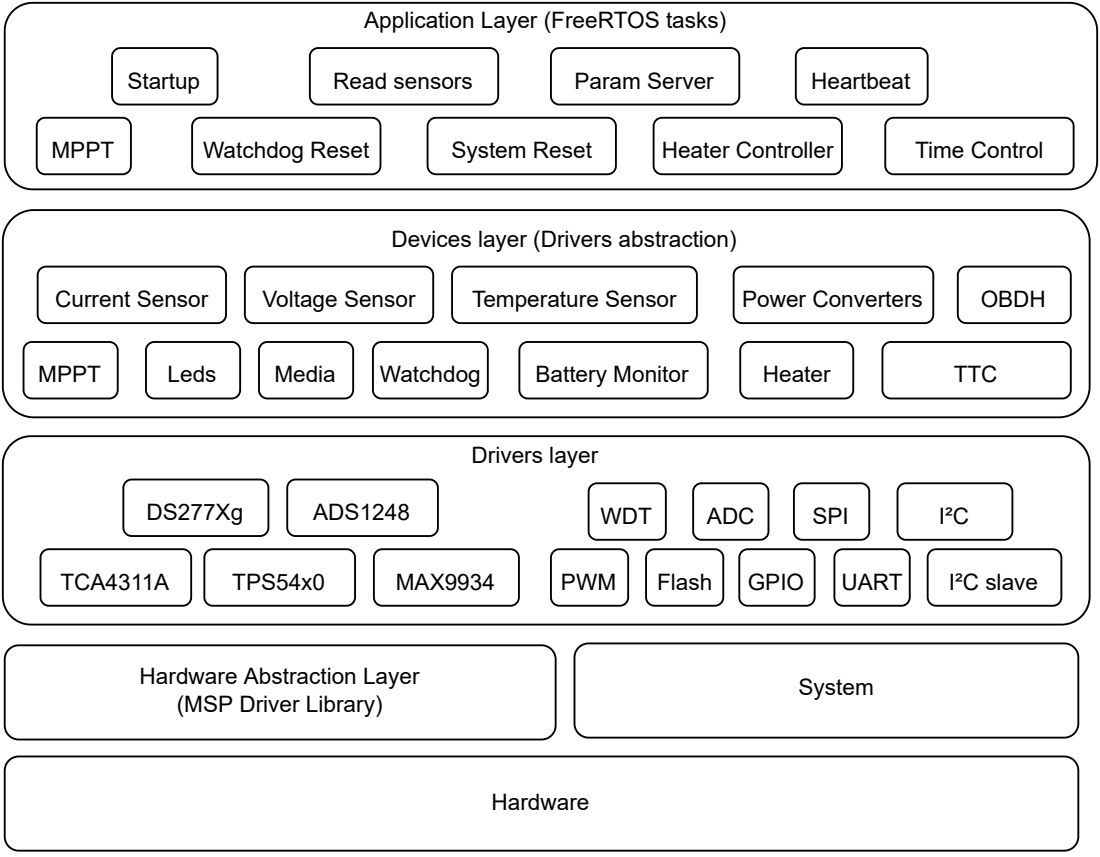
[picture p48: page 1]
Hardware; Drivers layer; ADS1248; ADC; SPI; MAX9934; GPIO; UART; TCA4311A; TPS54x0; Flash; I²C slave; I²C; Battery Monitor; Current Sensor; MPPT; Leds; Media; Voltage Sensor; Temperature Sensor; OBDH; TTC; WDT; Watchdog; Startup; Watchdog Reset; System Reset; Heater Controller; Read sensors; Time Control; Param Server; Power Converters; Heater; Heartbeat; PWM; System

Application Layer (FreeRTOS tasks)

Devices layer (Drivers abstraction)

Hardware Abstraction Layer
(MSP Driver Library)

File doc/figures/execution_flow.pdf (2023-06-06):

Transmit/Receive Data; Initialize sensors and microcontroller; Operation started; Yes; Initialize the MPPT controller; Initialize battery's monitoring system; Read sensors; System reset

Initialize heater's
on-off controller

Update the
heater's on-off
controller and
MPPT controller

Communication request
from OBDH/TTC?

Is the system on
for more than 10h?

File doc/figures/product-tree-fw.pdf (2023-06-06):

Drivers; Devices; Tasks; ADC; ADS1248; Flash; GPIO; I2C (Master); I2C (Slave); PWM; MAX9934; TPS54x0; UART (TX); SPI; TCA4311A; Battery Monitor; Current Sensor; Heater; LED; Media; MPPT; Power Converter; Temperature Sensor; Voltage Sensor; Watchdog; Command Server; Heartbeat; Heater Controller; MPPT Algorithm; Parameters Server; Read Sensors; Startup; System Reset; Time Control; Watchdog Reset; EPS 2.0 Firmware; RTOS; Tests; FreeRTOS; HAL; DriverLib; System; Clocks; Hooks; Setup; Log; Mockups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

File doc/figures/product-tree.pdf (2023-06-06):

EPS 2.0; Hardware; Firmware; Documentation; Interface Control Document (ICD); Design Definition File (DDF); Block Diagram; Schematics; PCB Layout; HAL; Drivers; Devices; RTOS; System; Tasks; Tests; Assembly Instructions; V&V Procedure; Usage Instructions

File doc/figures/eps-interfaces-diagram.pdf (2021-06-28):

Battery Board 4C | OBDH

EPS 2.0; Radio 0 MCU (TTC); Desktop (Log messages); B2-I²C; A2-UART; A0-UART; SBW-4: Tx SBW-5: Rx or UART-1: Tx UART-2: Rx; H2-49: SDA H2-51: SCL; ADS1248; A1-SPI; External Interface (IIP) JTAG; SBW

RTD2 PicoBlade
2-wire four RTDs
measurements

USB log messages

Note: all comunication
channels goes to EPS2 MCU

H2-5: EPS Tx Beacon Rx
H2-7: EPS Rx Beacon Tx

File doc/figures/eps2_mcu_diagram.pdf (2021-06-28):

EPS 2.0; Microcontroller MPPT Subsystem; Power Converters Subsystem; Batteries Management Subsystem; Solar Panel Boards; Kill-Switches and RBF; JTAG; UART; ADC x9; PWM x3; PWM x2; I²C; SPI; ADC x3; GPIO x2; GPIO x3; POWER; Solar Panels Input; Batteries Daughterboard; Debugging Interface; VBUS; Gate control; External charger; Batteries Charge Connector; Versioning Resistors; Charger Input; I²C Buffer; optional I²C slave

Batteries power and measurments

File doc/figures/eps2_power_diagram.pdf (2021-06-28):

Solar Panel Boards; Maximum Power Point Tracking (MPPT) Subsystem; Batteries Daughterboard; Power Converters Subsystem; Current Measurement -Y; Current Measurement +X; Current Measurement -X; Current Measurement +Z; Current Measurement -Z; Current Measurement +Y; MPPT Boost -Y +X; MPPT Boost -X +Z; MPPT Boost -Z +Y; Voltage Measurement -Y +X; Voltage Measurement -X +Z; Voltage Measurement -Z +Y; Solar Panels Kill-Switches; Voltage; Measurement; Batteries; Kill-Switches; Voltage Measurement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

*Full charge voltage and maximum current discharge of 4 cell battery pack

Batteries Management Subsystem



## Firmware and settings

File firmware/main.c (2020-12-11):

/*
 * main.c
 * 
 * Copyright (C) 2019, SpaceLab.
 * 
 * This file is part of EPS 2.0.
 * 
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
 */

/**
 * \brief Main file.
 * 
 * \author Gabriel Mariano Marcelino <gabriel.mm8@gmail.com>
 * 
 * \version 0.1.0
 * 
 * \date 2020/10/21
 * 
 * \defgroup main Main file
 * \{
 */

#include <FreeRTOS.h>
#include <task.h>

#include "devices/watchdog/watchdog.h"
#include "system/clocks.h"
#include "app/tasks/tasks.h"

void main(void)
{
    /* Watchdog device initialization */
    watchdog_init();

    /* System clocks configuration */
    clocks_setup((clocks_config_t){.mclk_hz = 32000000UL, .smclk_hz=32000000UL, .aclk_hz=32768});

    /* Create all the tasks */
    create_tasks();

    /* Start the scheduler */
    vTaskStartScheduler();

    /* Will only get here if there was insufficient memory to create the idle and/or timer task */
    while(1);
}

/** \} End of main group */

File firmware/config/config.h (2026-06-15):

/*
 * config.h
 * 
 * Copyright The EPS 2.0 Contributors.
 * 
 * This file is part of EPS 2.0.
 * 
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
 */

/**
 * \brief Configuration parameters definition.
 * 
 * \author Gabriel Mariano Marcelino <gabriel.mm8@gmail.com>
 * \author Augusto Cezar Boldori Vassoler <augustovassoler@gmail.com>
 * \author João Cláudio Elsen Barcellos <joaoclaudiobarcellos@gmail.com>
 * \author Ramon de Araujo Borba <ramonborba97@gmail.com>
 * 
 * \version 0.4.0
 * 
 * \date 2021/01/25
 * 
 * \defgroup config Configuration
 * \{
 */

#include "system/sys_log/sys_log.h"

#ifndef CONFIG_H_
#define CONFIG_H_

/* System */
#define CONFIG_GLOBAL_LOG_LEVEL                         SYS_LOG_INFO

/* Tasks */
#define CONFIG_TASK_STARTUP_ENABLED                     1
#define CONFIG_TASK_WATCHDOG_RESET_ENABLED              1
#define CONFIG_TASK_HEARTBEAT_ENABLED                   1
#define CONFIG_TASK_SYSTEM_RESET_ENABLED                1
#define CONFIG_TASK_READ_SENSORS_ENABLED                1
#define CONFIG_TASK_PARAM_SERVER_ENABLED                1
#define CONFIG_TASK_MPPT_ALGORITHM_ENABLED              1
#define CONFIG_TASK_HEATER_CONTROLLER_ENABLED           1
#define CONFIG_TASK_TIME_CONTROL_ENABLED                1
#define CONFIG_TASK_DEVICE_RESPONSE_ENABLED             1

/* Tasks Debug Logs*/
#define CONFIG_TASK_READ_SENSORS_DEBUG_ENABLED          0

/* Devices */
#define CONFIG_SET_DUMMY_EPS                            0
#define CONFIG_DEV_LEDS_ENABLED                         1
#define CONFIG_DEV_HEATER_ENABLED                       1
#define CONFIG_DEV_MPPT_ENABLED                         1
#define CONFIG_DEV_BAT_MANAGER_ENABLED                  0
#define CONFIG_DEV_BATTERY_MONITOR_ENABLED              1
#define CONFIG_DEV_MEDIA_ENABLED                        1
#define CONFIG_DEV_CURRENT_SENSOR_ENABLED               1
#define CONFIG_DEV_VOLTAGE_SENSOR_ENABLED               1
#define CONFIG_DEV_TEMP_SENSOR_ENABLED                  1
#define CONFIG_DEV_OBDH_ENABLED                         1
#define CONFIG_DEV_TTC_ENABLED                          1
#define CONFIG_DEV_POWER_CONV_ENABLED                   1

/* Drivers */
#define CONFIG_DRIVERS_DEBUG_ENABLED                    0

/* List of parameter IDs to send as beacon packet. */
#define BEACON_PARAM_ID_LIST                            \
        EPS2_PARAM_ID_TIMESTAMP,                        \
        EPS2_PARAM_ID_MCU_TEMP,                         \
        EPS2_PARAM_ID_EPS_CURRENT,                      \
        EPS2_PARAM_ID_RESET_COUNTER,                    \
        EPS2_PARAM_ID_SP_MY_PX_VOLTAGE,                 \
        EPS2_PARAM_ID_SP_MX_PZ_VOLTAGE,                 \
        EPS2_PARAM_ID_SP_MZ_PY_VOLTAGE,                 \
        EPS2_PARAM_ID_SP_MY_CURRENT,                    \
        EPS2_PARAM_ID_SP_PY_CURRENT,                    \
        EPS2_PARAM_ID_SP_MX_CURRENT,                    \
        EPS2_PARAM_ID_SP_PX_CURRENT,                    \
        EPS2_PARAM_ID_SP_MZ_CURRENT,                    \
        EPS2_PARAM_ID_SP_PZ_CURRENT,                    \
        EPS2_PARAM_ID_MPPT_1_DUTY_CYCLE,                \
        EPS2_PARAM_ID_MPPT_2_DUTY_CYCLE,                \
        EPS2_PARAM_ID_MPPT_3_DUTY_CYCLE,                \
        EPS2_PARAM_ID_SP_VOLTAGE_MPPT,                  \
        EPS2_PARAM_ID_MAIN_POWER_BUS_VOLTAGE,           \
        EPS2_PARAM_ID_RTD_0_TEMP,                       \
        EPS2_PARAM_ID_RTD_1_TEMP,                       \
        EPS2_PARAM_ID_RTD_2_TEMP,                       \
        EPS2_PARAM_ID_RTD_3_TEMP,                       \
        EPS2_PARAM_ID_RTD_4_TEMP,                       \
        EPS2_PARAM_ID_RTD_5_TEMP,                       \
        EPS2_PARAM_ID_RTD_6_TEMP,                       \
        EPS2_PARAM_ID_BAT_VOLTAGE,                      \
        EPS2_PARAM_ID_BAT_CURRENT,                      \
        EPS2_PARAM_ID_BAT_CHARGE,                       \
        EPS2_PARAM_ID_BAT_HEATER_1_DUTY_CYCLE,          \
        EPS2_PARAM_ID_BAT_HEATER_2_DUTY_CYCLE

/* Callsign */
#define CONFIG_SATELLITE_CALLSIGN                       " PY0EFS"   /* The callsign field must be 7 characters long! */

/* Packets IDs */
#define CONFIG_PKT_ID_BEACON                            0x00
    
/* Memory adresses */
#define CONFIG_MEM_ADR_SYS_TIME                         0

#define MAX_BATTERY_CHARGE                              2450    /* [mAh] */
#define BAT_MONITOR_CHARGE_VALUE                        (uint16_t)(MAX_BATTERY_CHARGE/0.625)    /* 0.625 is a conversion factor for the  battery monitor */
#define RESET_BATTERY_TO_INITIAL_STATE                  0

#endif /* CONFIG_H_ */

/** \} End of config group */

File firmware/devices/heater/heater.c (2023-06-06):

/*
 * heater.c
 *
 * Copyright (C) 2021, SpaceLab.
 *
 * This file is part of EPS 2.0.
 *
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
 */

/**
 * \brief Heater device implementation.
 *
 * \author Jo�o Cl�udio <joaoclaudiobarcellos@gmail.com>
 * \author Andr� M. P. de Mattos <andre.mattos@spacelab.ufsc.br>
 *
 * \version 0.2.27
 *
 * \date 2021/08/04
 *
 * \addtogroup heater
 * \{
 */

#include <system/sys_log/sys_log.h>

#include "heater.h"

pid_controller_t pid_controller;
heater_config_t heater_config;

int heater_init(heater_channel_t channel) 
{
    sys_log_print_event_from_module(SYS_LOG_INFO, HEATER_MODULE_NAME, "Initializing Heater device.");
    sys_log_new_line();   

    /* PID controller initialization */
    pid_controller.tau              = PID_TAU_INIT; 
    pid_controller.limMin           = PID_LIMIT_MINIMUM_INIT;    
    pid_controller.limMax           = PID_LIMIT_MAXIMUM_INIT;    
    pid_controller.limMinInt        = PID_LIMIT_MINIMUM_INTEGRATOR_INIT;        
    pid_controller.limMaxInt        = PID_LIMIT_MAXIMUM_INTEGRATOR_INIT;        
    pid_controller.sample_time      = PID_SAMPLE_TIME_INIT;
    pid_controller.integrator       = PID_INTEGRATOR_INIT;        
    pid_controller.prevError        = PID_PREVIOUS_ERROR_INIT;        
    pid_controller.differentiator   = PID_DIFFERENTIATOR_INIT;               
    pid_controller.prevMeasurement  = PID_PREVIOUS_MEASUREMENT_INIT;              
    pid_controller.out              = PID_OUTPUT_INIT;

    /* Initialize the PWM parameters */
    heater_config.period_us         = HEATER_PERIOD_INIT;
    heater_config.duty_cycle        = HEATER_DUTY_CYCLE_INIT;

    switch(channel){
        
        case HEATER_CONTROL_LOOP_CH_0:

            if(pwm_init(HEATER_CONTROL_LOOP_CH_SOURCE, HEATER_ACTUATOR_CH_0, heater_config))
            {
                sys_log_print_event_from_module(SYS_LOG_ERROR, HEATER_MODULE_NAME, "Error during the initialization (CH0)!");
                sys_log_new_line();
                return -1;
            }        
        
            break;

        case HEATER_CONTROL_LOOP_CH_1:

            if(pwm_init(HEATER_CONTROL_LOOP_CH_SOURCE, HEATER_ACTUATOR_CH_1, heater_config))
            {
                sys_log_print_event_from_module(SYS_LOG_ERROR, HEATER_MODULE_NAME, "Error during the initialization (CH1)!");
                sys_log_new_line();
                return -1;
            }

            break;

    }

    return 0;
}

float heater_algorithm(float setpoint, float measurement) 
{
    /* Error signal */
    float error = setpoint - measurement;

    /* Proportional: 
     * p[n]=Kp*e[n] 
     */
    float proportional = PID_PROPORTIONAL_CONSTANT*error;

    /* Integral: 
     * i[n]= ((Ki*T)/2)*(e[n]-e[n-1])+i[n-1] 
     */
    pid_controller.integrator += 0.5f * PID_INTEGRATOR_CONSTANT * pid_controller.sample_time * (error + pid_controller.prevError);

    /* Anti-wind-up via integrator clamping */
    if (pid_controller.integrator > pid_controller.limMaxInt) {

        pid_controller.integrator = pid_controller.limMaxInt;

    } else if (pid_controller.integrator < pid_controller.limMinInt) {

        pid_controller.integrator = pid_controller.limMinInt;

    }

    /* Derivative (band-limited differentiator): 
     * d[n]=(2*Kd*(e[n]-e[n-1])+(2*tau-T)*d[n-1])/(2*tau+T) 
     */
    pid_controller.differentiator = -(2.0f * PID_DIFFERENTIATOR_CONSTANT * (measurement - pid_controller.prevMeasurement)   /* Note: derivative on measurement, therefore minus sign in front of equation! */
                        + (2.0f * pid_controller.tau - pid_controller.sample_time) * pid_controller.differentiator)
                        / (2.0f * pid_controller.tau + pid_controller.sample_time);

    /*
     * Compute output and apply limits
     * out[n]=p[n]+i[n]+d[n]
     */
    pid_controller.out = proportional + pid_controller.integrator + pid_controller.differentiator;

    if (pid_controller.out > pid_controller.limMax) {

        pid_controller.out = pid_controller.limMax;

    } else if (pid_controller.out < pid_controller.limMin) {

        pid_controller.out = pid_controller.limMin;

    }

    /* Store error and measurement for later use */
    pid_controller.prevError       = error;
    pid_controller.prevMeasurement = measurement;

    /* Return controller output */
    return pid_controller.out;
}

int heater_get_sensor(heater_channel_t channel, temperature_t *temp) 
{   
    switch(channel) 
    {
        case HEATER_CONTROL_LOOP_CH_0:
            return temp_rtd_read_k(HEATER_SENSOR_CH_0, (uint16_t *)&temp);
        case HEATER_CONTROL_LOOP_CH_1:
            return temp_rtd_read_k(HEATER_SENSOR_CH_1, (uint16_t *)&temp);
        default:
            sys_log_print_event_from_module(SYS_LOG_ERROR, HEATER_MODULE_NAME, "Invalid sensor channel!");
            sys_log_new_line();
            return -1;
    }
}

int heater_set_actuator(heater_channel_t channel, float pid_output) 
{
    switch(channel) 
    {
        case HEATER_CONTROL_LOOP_CH_0:
            heater_config.duty_cycle = pid_output;
            if (pid_output == 0)
            {
                return pwm_stop(HEATER_CONTROL_LOOP_CH_SOURCE, HEATER_ACTUATOR_CH_0, heater_config);
            }
            else 
            {
                return pwm_update(HEATER_CONTROL_LOOP_CH_SOURCE, HEATER_ACTUATOR_CH_0, heater_config);
            }
        case HEATER_CONTROL_LOOP_CH_1:
            heater_config.duty_cycle = pid_output;
            if (pid_output == 0)
            {
                return pwm_stop(HEATER_CONTROL_LOOP_CH_SOURCE, HEATER_ACTUATOR_CH_1, heater_config);
            }
            else 
            {
                return pwm_update(HEATER_CONTROL_LOOP_CH_SOURCE, HEATER_ACTUATOR_CH_1, heater_config);
            }
        default:
            sys_log_print_event_from_module(SYS_LOG_ERROR, HEATER_MODULE_NAME, "Invalid actuator channel!");
            sys_log_new_line();
            return -1;
    }
}

/** \} End of heater group */

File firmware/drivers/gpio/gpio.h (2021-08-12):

/*
 * gpio.h
 * 
 * Copyright (C) 2019, SpaceLab.
 * 
 * This file is part of EPS 2.0.
 * 
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
 */

/**
 * \brief GPIO driver definition.
 * 
 * \author Gabriel Mariano Marcelino <gabriel.mm8@gmail.com>
 * 
 * \version 0.2.14
 * 
 * \date 2020/10/24
 * 
 * \defgroup gpio GPIO
 * \ingroup drivers
 * \{
 */

#ifndef GPIO_H_
#define GPIO_H_

#include <stdint.h>
#include <stdbool.h>

#define GPIO_MODULE_NAME    "GPIO"

#define GPIO_STATE_HIGH     (true)
#define GPIO_STATE_LOW      (false)

/**
 * \brief GPIO pins.
 */
typedef enum
{
    GPIO_PIN_0=0,           /**< GPIO pin 0. */
    GPIO_PIN_1,             /**< GPIO pin 1. */
    GPIO_PIN_2,             /**< GPIO pin 2. */
    GPIO_PIN_3,             /**< GPIO pin 3. */
    GPIO_PIN_4,             /**< GPIO pin 4. */
    GPIO_PIN_5,             /**< GPIO pin 5. */
    GPIO_PIN_6,             /**< GPIO pin 6. */
    GPIO_PIN_7,             /**< GPIO pin 7. */
    GPIO_PIN_8,             /**< GPIO pin 8. */
    GPIO_PIN_9,             /**< GPIO pin 9. */
    GPIO_PIN_10,            /**< GPIO pin 10. */
    GPIO_PIN_11,            /**< GPIO pin 11. */
    GPIO_PIN_12,            /**< GPIO pin 12. */
    GPIO_PIN_13,            /**< GPIO pin 13. */
    GPIO_PIN_14,            /**< GPIO pin 14. */
    GPIO_PIN_15,            /**< GPIO pin 15. */
    GPIO_PIN_16,            /**< GPIO pin 16. */
    GPIO_PIN_17,            /**< GPIO pin 17. */
    GPIO_PIN_18,            /**< GPIO pin 18. */
    GPIO_PIN_19,            /**< GPIO pin 19. */
    GPIO_PIN_20,            /**< GPIO pin 20. */
    GPIO_PIN_21,            /**< GPIO pin 21. */
    GPIO_PIN_22,            /**< GPIO pin 22. */
    GPIO_PIN_23,            /**< GPIO pin 23. */
    GPIO_PIN_24,            /**< GPIO pin 24. */
    GPIO_PIN_25,            /**< GPIO pin 25. */
    GPIO_PIN_26,            /**< GPIO pin 26. */
    GPIO_PIN_27,            /**< GPIO pin 27. */
    GPIO_PIN_28,            /**< GPIO pin 28. */
    GPIO_PIN_29,            /**< GPIO pin 29. */
    GPIO_PIN_30,            /**< GPIO pin 30. */
    GPIO_PIN_31,            /**< GPIO pin 31. */
    GPIO_PIN_32,            /**< GPIO pin 32. */
    GPIO_PIN_33,            /**< GPIO pin 33. */
    GPIO_PIN_34,            /**< GPIO pin 34. */
    GPIO_PIN_35,            /**< GPIO pin 35. */
    GPIO_PIN_36,            /**< GPIO pin 36. */
    GPIO_PIN_37,            /**< GPIO pin 37. */
    GPIO_PIN_38,            /**< GPIO pin 38. */
    GPIO_PIN_39,            /**< GPIO pin 39. */
    GPIO_PIN_40,            /**< GPIO pin 40. */
    GPIO_PIN_41,            /**< GPIO pin 41. */
    GPIO_PIN_42,            /**< GPIO pin 42. */
    GPIO_PIN_43,            /**< GPIO pin 43. */
    GPIO_PIN_44,            /**< GPIO pin 44. */
    GPIO_PIN_45,            /**< GPIO pin 45. */
    GPIO_PIN_46,            /**< GPIO pin 46. */
    GPIO_PIN_47,            /**< GPIO pin 47. */
    GPIO_PIN_48,            /**< GPIO pin 48. */
    GPIO_PIN_49,            /**< GPIO pin 49. */
    GPIO_PIN_50,            /**< GPIO pin 50. */
    GPIO_PIN_51,            /**< GPIO pin 51. */
    GPIO_PIN_52,            /**< GPIO pin 52. */
    GPIO_PIN_53,            /**< GPIO pin 53. */
    GPIO_PIN_54,            /**< GPIO pin 54. */
    GPIO_PIN_55,            /**< GPIO pin 55. */
    GPIO_PIN_56,            /**< GPIO pin 56. */
    GPIO_PIN_57,            /**< GPIO pin 57. */
    GPIO_PIN_58,            /**< GPIO pin 58. */
    GPIO_PIN_59,            /**< GPIO pin 59. */
    GPIO_PIN_60,            /**< GPIO pin 60. */
    GPIO_PIN_61,            /**< GPIO pin 61. */
    GPIO_PIN_62,            /**< GPIO pin 62. */
    GPIO_PIN_63,            /**< GPIO pin 63. */
    GPIO_PIN_64,            /**< GPIO pin 64. */
    GPIO_PIN_65,            /**< GPIO pin 65. */
    GPIO_PIN_66,            /**< GPIO pin 66. */
    GPIO_PIN_67,            /**< GPIO pin 67. */
    GPIO_PIN_68,            /**< GPIO pin 68. */
    GPIO_PIN_69             /**< GPIO pin 69. */
} gpio_pins_e;

/**
 * \brief GPIO modes.
 */
typedef enum
{
    GPIO_MODE_OUTPUT=0,     /**< GPIO as output. */
    GPIO_MODE_INPUT         /**< GPIO as input. */
} gpio_modes_e;

/**
 * \brief GPIO pin configuration.
 */
typedef struct
{
    uint8_t mode;
} gpio_config_t;

/**
 * \brief GPIO pin.
 */
typedef uint8_t gpio_pin_t;

/**
 * \brief Initialization routine of a GPIO pin.
 *
 * \param[in] pin is the GPIO pin to initialize.
 *
 * \param[in] config is the configuration to initialize the GPIO pin.
 *
 * \return The status/error code.
 */
int gpio_init(gpio_pin_t pin, gpio_config_t config);

/**
 * \brief Sets the state of a given output GPIO pin.
 *
 * \param[in] pin is the GPIO pin to set the state.
 *
 * \param[in] level is the new state of the given GPIO pin. It can be:
 * \parblock
 *      - GPIO_STATE_HIGH
 *      - GPIO_STATE_LOW
 *      .
 * \endparblock
 *
 * \return The status/error code.
 */
int gpio_set_state(gpio_pin_t pin, bool state);
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

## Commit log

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2020-05-01 hardware: schematics: interface: Improving and updating sheet organization
    [EPS_Interface.SchDoc]
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2020-05-01 hardware: schematics: interface: Updating PC104 I2C interface position
    [EPS_Interface.SchDoc]
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2020-05-03 hardware: schematics: battery_circuits: Improving sheet organization and adding monitor bypass resistor
    [2_Battery_Monitoring_And_Switches.SchDoc]
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2020-05-03 hardware: schematics: digital_circuits: Adding I2C buffer and updating harness
    [3_MCU_EPS.SchDoc]
2020-05-03 hardware: schematics: interface: Updating I2C signals and harness
    [EPS_Interface.SchDoc]
2020-05-03 hardware: schematics: digital_circuits: Adding RX capability to the UART Beacon interface
    [3_MCU_EPS.SchDoc]
2020-05-03 hardware: schematics: topology: Removing unnecessary connections and updating UART Beacon
    [EPS_Topology.SchDoc]
2020-05-03 hardware: schematics: interface: Updating UART Beacon interface and harness
    [EPS_Interface.SchDoc]
2020-05-03 hardware: schematics: heater_circuits: Improving sheet organization and labels
    [4_Battery_Heater_Controller.SchDoc]
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2020-05-03 hardware: schematics: Fixing compilation errors
    [7_dc_dc_3V3_3V3_Deployment_ANT.SchDoc, 8_dc_dc_5V_5A_Radio.SchDoc, Block_diagram.SchDoc]
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2020-05-04 hardware: libraries: Fixing the link of footprints and schematic symbols in the new components
2020-05-04 hardware: schematics: interface: Fixing antenna supply PC104 connection error
    [EPS_Interface.SchDoc]
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2020-05-04 hardware: schematics: battery_circuits: Fixing charger input connection
    [2_Battery_Monitoring_And_Switches.SchDoc]
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2020-05-10 hardware: schematics: power_converters: eps_beacon: Fixing Rsense3 connections
    [5_dc_dc_3V3_EPS_Beacon.SchDoc]
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2020-07-08 hardware: libraries: Refreshing the schematic library with new parameters in components and adding missing ones #3
2020-07-08 hardware: schematics: Refreshing all project schematics with new parameters from schematic library #3
    [1_Measurement_and_MPPT.SchDoc, 2_Battery_Monitoring_And_Switches.SchDoc, 3_MCU_EPS.SchDoc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]
2020-07-08 hardware: schematics: Substitution of obsolete components corresponding to C62, C77, C78, Q1 and Q2 designators.
    [1_Measurement_and_MPPT.SchDoc, 3_MCU_EPS.SchDoc, 4_Battery_Heater_Controller.SchDoc]
2020-07-13 hardware: libraries & schematic: Fixing missing comment from schematic library on 3k3 resistor and updating 1_Measurement_and_MPPT schematic sheet #5
    [1_Measurement_and_MPPT.SchDoc]
2020-07-15 hardware: libraries & schematic: Fixing missing comment and footprint from schematic library on 1k resistor and updating 4_Battery_Heater_Controller schematic sheet #5
    [4_Battery_Heater_Controller.SchDoc]
2020-07-17 Hardware: libraries & pcb: fixing 3d model on pcb and schematic libraries and updating the pcb close #7
2020-07-17 hardware: schematic & pcb: adding another battery connector for cross-compatible between different battery board versions close #13
    [EPS_Interface.SchDoc]
2020-07-17 hardware: libraries & schematic & pcb: Adding fiducials schematic symbol and footprints to libraries, adding components to Block_Diagram schematic and positioned them on the pcb close #11
    [Block_diagram.SchDoc]
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2020-07-22 hardware: variants: Done initial variants "Test Model" and "Flight Model" with found DNP components on schematics #9
    [PCB_Project_FlightModel_EPS.PrjPcb]
2020-07-22 hardware: variants: draftsman: Adding draftsman file (.PCBDwf) to project with top and bottom assembly of not fitted components #9
    [PCB_Project_FlightModel_EPS.PrjPcb]
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2020-09-01 hardware: schematics: Updating signal names and beacon output voltage to 6V #16
    [0_architecture.schdoc, 1_interface.schdoc, 2_topology.schdoc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]
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2020-09-01 hardware: Updating project file to include the path for the newer outputs
    [eps2_project.prjpcb]
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2020-09-06 hardware: sources: Updating architecture schematic sheet with separate power and mcu diagrams close #17
    [0_architecture.schdoc]
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2020-09-06 hardware: sources: Fixing missing "Partnumber" parameter on 3k3 and 4k7 resistors for BOM generation #19
    [3_measurement_and_mppt.schdoc, 5_mcu_main.schdoc]
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2020-09-06 hardware: outputs: board_bom: Adding final BOM file using the newer SpaceLab template and deleting the old one present on the directory close #19
    [board_bom.xls, board_bom.xlsx]
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2021-01-17 firmware: drivers: onewire: adding gpio_get_state to reset function #25
    [onewire.c]
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2021-01-19 firmware: drivers: ads1248: Adding ADS1248_RESET status, ads1248_delay function, updating ads1248_init and first version of the reset function #29
    [ads1248.c]
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2021-01-22 firmware: drivers: ads1248: Adding power-down modes to header and arguments to its function, updating init function, simplifying reset, first version of powerdown and write_cmd with registers values 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
    [ads1248.c]
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2021-02-01 firmware: fixing bat_manager device, ds2775g and onewire drivers wrong paramaters #32
    [ds2775g.c, onewire.c]
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2021-02-02 hardware: fabrication: Adding missing BOM file close #67
    [board_bom.xlsx]
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2021-02-03 hardware: Adding new draftsman source file to project tree and modifying DNP components on variants close #9
    [eps2_project.prjpcb]
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2021-02-03 firmware: devices: fixing ADC ports defines
    [current_sensor.h, voltage_sensor.h]
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2021-02-10 hardware: sources: Improving status leds net labels and silkscreen labels close #72
    [4_battery_monitoring_and_switches.schdoc, 7_dc_dc_3v3_eps_ttc.schdoc, 7_dc_dc_5v_payloads.schdoc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]
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2021-02-13 firmware: drivers: ads1248: Down-grading version control, adding missing separate delay function and "overkill" reset pulse duration #29
    [ads1248.c]
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2021-02-26 hardware: boms: Updating bill of materials with new template in the outputs and fabrication folders
    [board_bom.xlsx]
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2021-02-26 hardware: images: Deleting unnecessary diagrams, adding their latest source files from documentation and updating the architecture schematic sheet
    [0_architecture.schdoc]
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2021-03-08 hardware: sources and outputs: Changing PCB solder mask for a better green color, updating SpaceLab logo on pcb layout, updating outjob new color of 3D prints and regenerating full PDF now with fixed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
    [eps2_project.prjpcb]
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2021-03-10 firmware: drivers: ads1248: Removing unnecessary select slave function, adding ADS1248 functionality to change the ADC positive channel of measurement, ajusting functions parameters and defining fixe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
    [ads1248.c]
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2021-03-23 firmware: fixing current and voltage sensor devices #64 #65
    [current_sensor.c, current_sensor.h, max9934.c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]
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2021-04-03 hardware: sources: Updating MCU and power diagrams on architecture schematic sheet close #97
    [0_architecture.schdoc]
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2021-04-10 firmware: app: structs: Fixing missing semicolons. firmware: app: tasks: Fixing undeclared statements of FreeRTOS, adding read sensors task to tasks.c
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2021-04-21 doc: chapters: instructions: Adding first informations regarding powering up the EPS module #105 doc: chapters: hardware and system_overview: fixing labels
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2021-04-22 firmware: devices: ttc: correcting header informations #76
    [ttc.c]
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2021-04-24 firmware: app: tasks: Adding initial read sensors task with voltage and current readings of the solar panels, solar panels total output voltage, main power bus voltage and EPS MCU and Beacon DC-DC bu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
    [voltage_sensor.c, voltage_sensor.h]
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2021-05-16 hardware: sources: Adding pin header jumper for JTAG and 3V3 DC-BUCK MCU power separation #38
    [1_interface.schdoc]
2021-05-16 hardware: sources: Renaming dedicated DC-DC buck converter net labels for the radio transceivers power close #111
    [2_topology.schdoc, 7_dc_dc_5v_radios.schdoc]
2021-05-16 hardware: sources: Changing shunt and output resistors of the solar panels current sensor circuits #103
    [3_measurement_and_mppt.schdoc]
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2021-05-24 hardware: sources: Changing heater, kill-switches, battery charger, JTAG and RTD picoblades to right angle version close #99
    [1_interface.schdoc, eps2_project.prjpcb]
2021-05-28 firmware: devices: Fixing system led pin and removing non-existent fault led
    [leds.c]
2021-06-01 firmware: hal: Correct comment
    [usci_b_i2c.c]
2021-06-01 firmware: drivers: ds2775g: fix include path
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2021-06-03 firmware: drivers: i2c_slave: Fixing version control
    [i2c_slave.c]
2021-06-03 firmware: devices: bat_manager: Fixing compilation error and include #32
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2021-06-03 firmware: drivers: onewire: Fixing missing colon and include of intrinsics library #25
    [onewire.c]
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2021-06-06 hardware: sources: Fixing Rout values for current sensing circuits #103
    [3_measurement_and_mppt.schdoc]
2021-06-07 hardware: prjpcb: Including 2 pin power selection JTAG header to flight model variant close #118
    [eps2_project.prjpcb]
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2021-06-07 firmware: drivers and devices: Improving adc driver and fixing voltage reference to 2.5V, updating voltage sensor device #64
    [adc.h, voltage_sensor.c, voltage_sensor.h]
2021-06-10 firmware: devices: temp_sensor: Adding missing functions to read internal mcu temperature (from obdh2), adding function prototypes for ads1248 readings in oC and kelving #33
    [temp_sensor.c, temp_sensor.h]
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2021-06-10 firmware: drivers: tps54x0: fix init function return value #31
    [tps54x0.c]
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2021-06-10 firmware: drivers: tps54x0: fix parameters types #31
    [tps54x0.c]
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2021-06-11 firmware: drivers: onewire: Temporarily fixing clock define #25
    [onewire.c]
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2021-06-12 firmware: devices: temp_sensor: Fixing function names for internal mcu temperature readings #33
    [temp_sensor.c, temp_sensor.h]
2021-06-12 firmware: devices: bat_manager: Fixing onewire_port argument and minor improviments to comments #32
2021-06-12 firmware: devices: current_sensor: Adding log message to initilization and fixing reference voltage argument name #65
    [current_sensor.c, current_sensor.h]
2021-06-14 firmware: app: tasks: Adding the periodic watchdog reset task
    [config.h]
2021-06-15 firmware: devices: leds: Fixing the LED device initialization
    [leds.c]
2021-06-15 firmware: app: tasks: Adding a periodic system reset task #55
    [config.h]
2021-06-15 firmware: drivers: i2c_slave: Fix I2C_PORT_1 pins
    [i2c_slave.c]
2021-06-15 hardware: layout: Fixing capacitors polarity indication. close #96
2021-06-15 hardware: libraries: Adding blocking diode of 2A to libraries hardware: sources: Updating component in schematic and layout #45 close #44
    [3_measurement_and_mppt.schdoc]
2021-06-15 hardware: libraries: Adding 0602 red led component hardware: sources: Adding system fault led to schematics and layout close #78
    [5_mcu_main.schdoc]
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2021-06-16 hardware: sources: schematics: Changing partnumber of IC, adding pull up for I²C, updating pin assigment to MCU and harness, removing 1-wire net label hardware: sources: layout: Preliminary component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
    [1_interface.schdoc, 2_topology.schdoc, 4_battery_monitoring_and_switches.schdoc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]
2021-06-16 hardware: libraries: Adding missing footprint to components from old floripasat library, adding DS2777G+ component
2021-06-16 hardware: sources: Updating the battery monitor circuitry and minor bugfixes
    [1_interface.schdoc, 4_battery_monitoring_and_switches.schdoc, 5_mcu_main.schdoc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]
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2021-06-22 firmware: devices: power_conv: Add error log to init function #120
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2021-06-29 firmware: drivers: Removing legacy code and fixing typos #24
    [ds2775g.c, pwm.c]
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2021-07-01 doc: chapters: hardware: Updating battery monitor schematic image, fixing size of figures #130
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2021-07-13 firmware: devices: obdh: Adding missing bracket
    [obdh.c]
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2021-07-16 firmware: Fix compilation errors
    [i2c_slave.c, ttc.c]
2021-07-16 firmware: drivers: Fixing implicit declaration issue
2021-07-16 firmware: devices: obdh: Fix compilation errors
    [obdh.c]
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2021-07-23 firmware: Fixing compilation errors and warnings
    [ads1248.c]
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2021-07-30 firmware: drivers: ads1248: Fixing undefined references due to lack of library
    [ads1248.c]
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2021-08-02 firmware: drivers: uart_interrupt: Fixing struct references and buffer declaration #140
    [uart_interrupt.c]
2021-08-02 firmware: devices: ttc: Fixing pointer assignments and function declaration #76
    [ttc.c]
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2021-08-03 firmware: drivers: pwm: Fixing period and duty cycle resolution #114
    [pwm.c]
2021-08-03 firmware: drivers: pwm: Fixing conversion to micro seconds #114
    [pwm.c]
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2021-08-04 firmware: Fixing typos and code style
    [ads1248.c, mppt.c, obdh.c]
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2021-08-06 firmware: drivers: gpio: Fixing typos
    [gpio.h]
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2021-08-12 firmware: drivers: uart_interrupt: Fixing the module name in the log routines #140
    [uart_interrupt.c]
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2021-08-12 firmware: app: tasks: heater_controller: Adding switch break after any error #142
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2021-08-12 firmware: devices: heater: Fixing typecast warning #73
    [heater.c]
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2021-08-12 firmware: drivers: ads1248: Fixing pointer calls #29
    [ads1248.c]
2021-08-12 firmware: drivers: uart_interrupt: Adding buffer index limit and fixing flag number #140
    [uart_interrupt.c]
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2021-08-12 firmware: devices: Fixing buffer declaration and adding variables copy #75 #76
    [obdh.c, ttc.c]
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2021-08-23 firmware: drivers: ads1248: Fixing buffer size, start pin pulse and adding sync command to reading function #29
    [ads1248.c]
2021-08-23 devices: temp_sensor: Fixing spi mode and cs pin #33
    [temp_sensor.h]
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2021-08-31 firmware: drivers: ds2777g: Fix operation on current raw value conversion.
2021-08-31 firmware: drivers: ds2777g: Add accumulated current read functions. Fix erros.
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2021-10-02 firmware: drivers: ds277Xg: Fix compilation errors
    [config.h, ds277Xg.c]
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2021-10-03 firmware: drivers: ds277Xg: Fix typo
    [ds277Xg.c]
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2021-10-03 firmware: app: tasks: read sensors: Fix compilation error
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2021-11-09 firmware: drivers: Fixing an invalid argument
    [ads1248.c]
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2021-12-01 firmware: Fixing bugs in the i2c communication
    [config.h, i2c_slave.c, obdh.c]
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2021-12-02 firmware: devices: obdh: Fixing the OBDH device #59
    [obdh.c]
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2021-12-07 firmware: drivers: i2c: Fixing the name of the initialization function
    [i2c.c]
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2021-12-07 firmware: drivers: i2c_slave: Fixing the interruption initialization
    [i2c_slave.c]
2022-03-09 firmware: app: tasks: Fixing the heater controller task #142
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2022-05-31 firmware: devices: ttc: Fixing the CRC calculation
    [ttc.c]
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2022-06-01 firmware: drivers: ds277xg: Fixed copy data to EEPROM command #157
    [ds277Xg.c]
2022-06-08 firmware: drivers: ds277xg: Fixed configuration preprocessor defines #157
    [config.h, ds277Xg.c]
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2022-06-08 firmware: drivers: ds277Xg: Added error verification to i2c initialization and fixed 'cycles' pointer assignment
    [ds277Xg.c]
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2022-06-14 firmware: drivers: ads1248: Fixing the way that the ADS1248's registers are configured and read #29
    [ads1248.c]
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2022-06-17 firmware: drivers: ds277Xg: Added more #defined parameter to avoid 'magic numbers' #157
    [ds277Xg.c]
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2022-06-17 firmware: drivers: ds277Xg: Corrected author emails #157
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2022-07-06 Add unfinised unit test for the bat_manager device; Add ttc_test (ttc_decode fails unexpectedly, so it's commented out for now)
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2022-07-20 firmware:drivers:ads1248: Fixed configuration registers and used commands to control de device #29
    [ads1248.c]
2022-07-20 firmware:drivers:ads1248: Fixed spi_transfer_no_cs function calls #29
    [ads1248.c]
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2022-07-20 firmware:drivers:ads1248: Fixed minor warnings #29
    [ads1248.c]
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2022-07-24 firmware: drivers: uart_interrupt: add missing semicolon
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2022-08-05 firmware: devices: temp_sensor: Fixed temperature conversion #33
    [temp_sensor.c]
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2022-08-24 firmware: tests: devices: Fix heater test to reflect changes made on pwm_wrap
2022-09-21 firmware: tests: devices: mppt_test: Fix incorrect variable assignment to previous duty cycle measurments
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2022-09-21 firmware: devices: power_conv: Fix payload enable pin
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2023-02-14 firmware: Fixing the UART functioning
    [ttc.c, uart_interrupt.c]
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2023-03-14 firmware: Fixing errors related to the communication with TTC
    [config.h]
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2023-07-04 firmware: devices: mppt: Fixed mppt channel indexing #193
    [mppt.c]
2023-07-04 firmware: devices: mppt: Fixed update_step function not storing the previous step #193
    [mppt.c]
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2023-07-12 firmware: app: tasks: Fix device response task buffer assignment
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2023-07-17 firmware: devices: mppt: Fixed power calculation truncating the result #193
    [mppt.c]
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2023-07-29 firmware: app: tasks: Fixed read sensors task logs to correctly print negative current values
    [config.h]
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2023-08-14 firmware: drivers: ds277Xg: Refactored ds277Xg init function to correctly set all the configuration registers #157
    [ds277Xg.c]
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2023-08-14 firmware: devices: battery_monitor: Added functions to read missing result registers #157
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2024-08-18 fix: Write MPPT duty cycle to the eps data structure in automatic mode
    [mppt.c, mppt.h]
2024-08-18 fix: Read sensors task writes correct data to the structure
2024-08-28 fix: Change bat charge parameter to mirror the accumulated current parameter
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2024-09-23 firmware: app: tasks: Fix beacon flag logic in device response task
2024-09-23 firmware: app: tasks: Fix media device init
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2024-09-29 fix: correct the beacon packet format
    change "time_counter" and "time_counter_ms" to "timestamp"
    add a ID for the beacon packet
    add the callsign
    [config.h]
2024-10-08 fix: resolve errors supposedly caused by the use of dynamic allocation
    [config.h]
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2025-08-23 firmware: drivers: i2c_slave: Fix RX buffer control inside irq handler
    [i2c_slave.c]
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

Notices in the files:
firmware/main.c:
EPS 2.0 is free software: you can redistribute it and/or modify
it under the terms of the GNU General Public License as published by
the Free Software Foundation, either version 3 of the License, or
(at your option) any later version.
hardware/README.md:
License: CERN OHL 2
